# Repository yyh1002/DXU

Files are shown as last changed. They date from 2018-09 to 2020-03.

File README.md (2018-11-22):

# DXU - Dual Extrusion Upgrade for Ultimaker 2+

### DISCUSSION:
https://community.ultimaker.com/topic/24553-dxu-another-dual-extrusion-upgrade-for-um2/

### UPDATES:
- 19 Nov 2018 - Moved the lever dock from front to the back. 

### CREDITS:

##### Hardware:  
Lever action is inspired by Ultimaker 3.   
##### Firmware:   
Modified based on Mark2 version of Tinkergnome firmware by Tinkergnome.  
##### Software:   
Used Mark2Tweaks plugin for CURA by Krys Lawrence. CURA profiles are modified based on the Mark2 profiles by Tinkergnome and foehnsturm.

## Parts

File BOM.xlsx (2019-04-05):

Bill of Material 物料清单
物品/Material |  | 数量/Quantity | 链接/Link | 选项/Option | 备用链接/Alternative Link
胖子UM2 1.75热端新直通套件 | UM2 1.75 Hotend Kit (Heatsink, Bowden Coupler) | 2 | https://item.taobao.com/item.htm?spm=a1z10.5-c.w4002-9918354853.34.576d75aec3Kk6M&id=521401997290 | 新直通套件 | https://www.aliexpress.com/store/product/3D-Printer-Upgrade-Ultimaker-2-UM2-Extended-Newest-Olsson-Block-Nozzle-Hot-end-Kit/1877169_32988128287.html
胖子UM2 1.75热端新直通加热块 | UM2 1.75 Hotend Heat Block | 2 | https://item.taobao.com/item.htm?spm=a1z10.5-c.w4002-9918354853.34.576d75aec3Kk6M&id=521401997290 | 新直通加热块
290度高温打印PI喉管垫片 2*4*1 | 290°C High Temp Print Hotend Insulator 2*4*1 | 2 | https://item.taobao.com/item.htm?spm=a1z10.5-c.w4002-9918354853.25.60724c2fxu3tfa&id=581596714621 | 小2*4*1
UM2加热棒 | UM2 Heater Cartridge | 2 | https://www.makerpoint.nl/nl/ultimaker-heater-cartridge-24v-35w-um2um2ext.html
UM2 PT100测温 | UM2 PT100 Sensor | 2 | https://www.makerpoint.nl/nl/ultimaker-pt100-b-sensor-glassfiber-um2um2ext.html
2*6.35四氟远程送料管 | 2*6.35 PTFE Bowden Tube | 2 | https://item.taobao.com/item.htm?spm=a1z10.5-c.w4002-9918354853.32.576d75aec3Kk6M&id=521852878986 | 2*6.35
6.35料管蓝白卡扣 | 6.35 Bowden Coupler | 2 | https://www.makerpoint.nl/nl/ultimaker-bowden-tube-clips-pack-ultimaker.html
1.75耗材挤出机 | 1.75 Filament Feeder | 2 | https://www.thingiverse.com/thing:2289203 | Use 2.85 version for 6.35 tube
NEMA17 42*48挤出机电机 | NEMA17 42*48 Stepper Motor | 1 | https://www.makerpoint.nl/nl/ultimaker-feeder-motor-um3-extended-assembly.html
3510 12v涡轮吹料风扇 | 3510 12v Blower Fan | 2 | https://au.mouser.com/ProductDetail/?qs=%2FW4LtXOBxKsfL3eA88psUg== |  | https://item.taobao.com/item.htm?id=538704495777&_u=t2dmg8j26111&qq-pf-to=pcqq.group
3010 5v热端散热风扇 | 3010 5v Hotend Cooling Fan | 1 | https://www.aliexpress.com/item/DC-Cooling-Fan-3010-Fan-30-30-10mm-3010-fans-5V-12V-24V-Suitable-for-extruders/32909524999.html | 3010-5v
直线轴承LM6LUU 6*12*35mm | Linear Bearing LM6LUU 6*12*35mm | 2 | https://sg.misumi-ec.com/vona2/detail/110302578040/
压缩弹簧 0.8*9*15 或近似（建议买几个不同粗细的） | Compression Spring 0.8*9*15 or similar | 1
M3*6平头螺丝 | M3*6 Countersunk Screw | 4 | https://www.mcmaster.com/92125A126
M3*16半圆头螺丝 | M3*16 Button Head Screw | 6 | https://www.mcmaster.com/92095A184
M3*20半圆头螺丝 | M3*20 Button Head Screw | 2 | https://www.mcmaster.com/92095A185
M3*35半圆头螺丝 | M3*35 Button Head Screw | 4 | https://www.mcmaster.com/92095A201
M3螺母 | M3 Nut | 8 | https://www.mcmaster.com/90592A085
M3*3顶丝 | M3*3 Set Screw Cup Head | 1 | https://www.mcmaster.com/91390A097

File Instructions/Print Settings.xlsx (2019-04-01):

Print Settings 打印设置
零件名称/Parts Name | 材料/Material | 层高/Layer Height | 外壁线数/Wall Line Count | 支撑/Support
01 Housing Front | PC or PA66 | 0.2 | 5 | NO
02 Housing Back
03 Fan Shroud 3510 |  |  |  | YES
04 Fan Cover 3010
11 Lever 1 |  | 0.1 | 5 | NO
12 Lever 2 |  |  |  | YES
13 Lever 3 |  |  |  | NO
21 Dock |  | 0.2 | 5 | NO
22 Dock liner | PLA |  |  | NO
31 Heater clamp a | PC or PA66 | 0.2 |  | NO
32 Heater clamp b
33 Hotend fan pusher

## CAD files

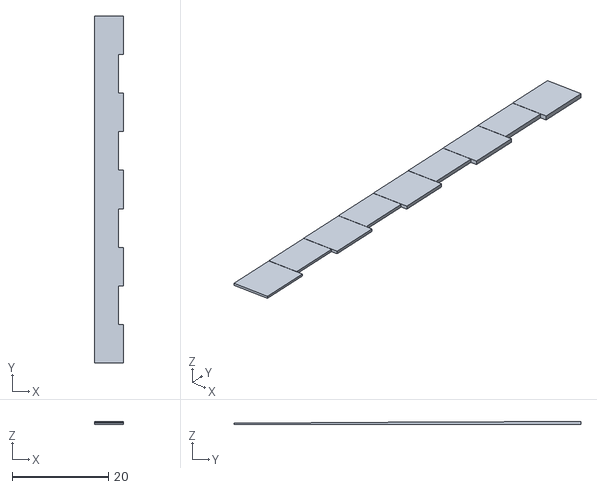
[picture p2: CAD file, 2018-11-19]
Calibration/Z-right.stl
6.00 x 72.0 x 0.66

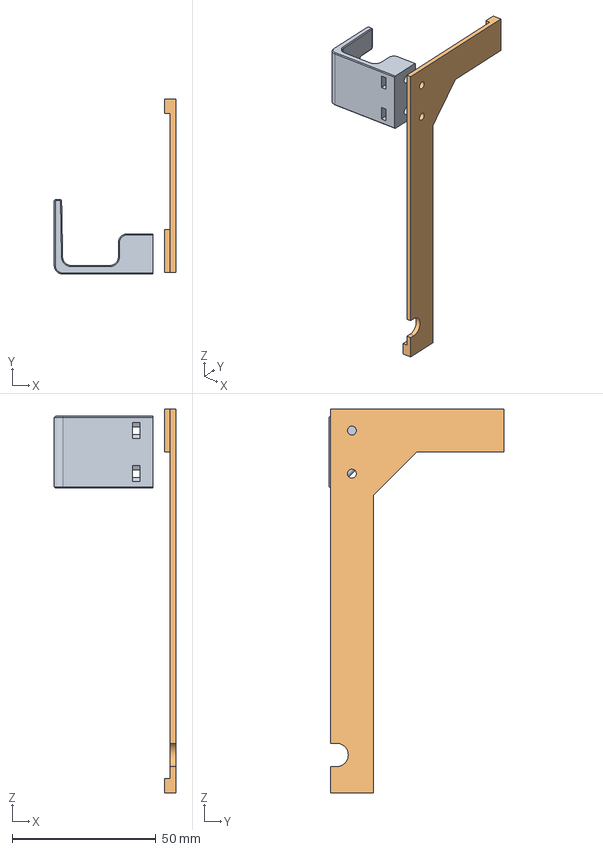
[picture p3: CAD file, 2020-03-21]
Parts file/Lever Dock Back.step
42.3 x 61.0 x 133.7 mm

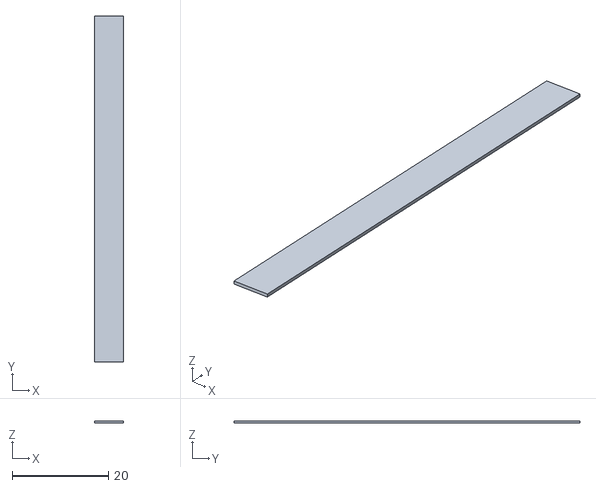
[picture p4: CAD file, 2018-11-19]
Calibration/Z-left.stl
6.00 x 72.0 x 0.5

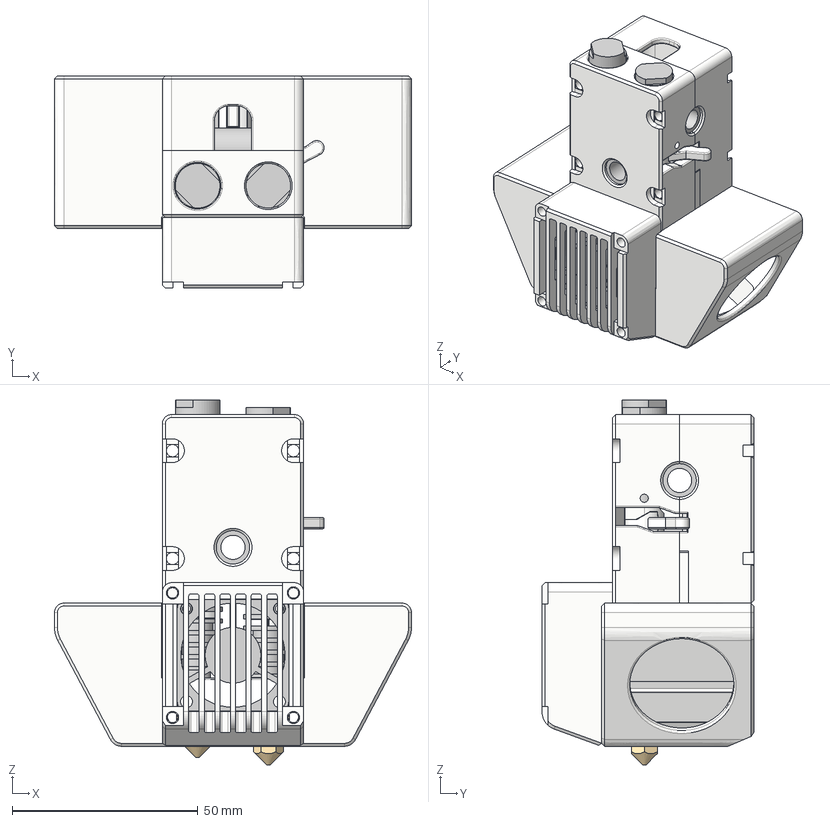
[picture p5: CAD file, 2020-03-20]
Parts file/DXU 1.5.step
96.0 x 57.0 x 98.1 mm
9434K51

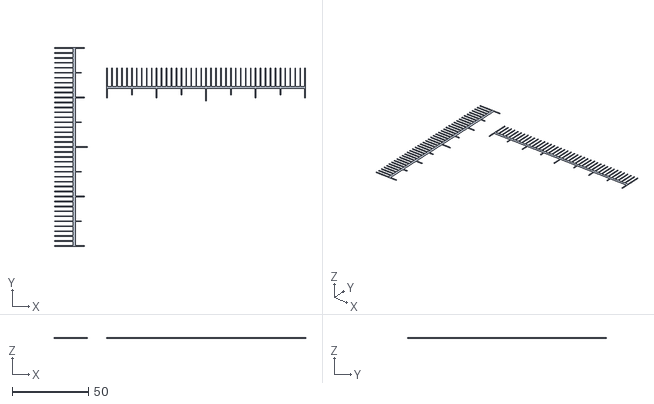
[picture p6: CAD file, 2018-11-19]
Calibration/xy_calibration_part_b.stl
164.3 x 130.1 x 0.3

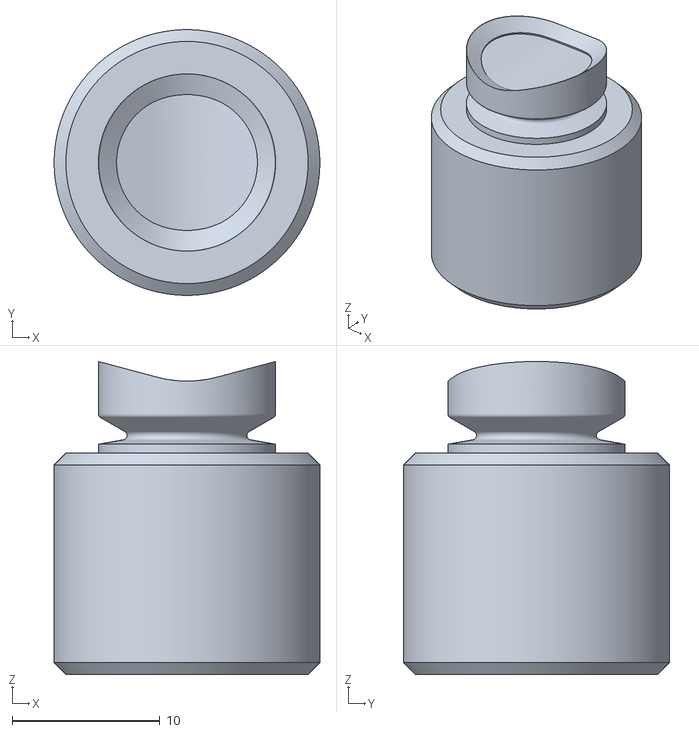
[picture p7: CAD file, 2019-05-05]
Parts file/46 Hole punch C.stl
18.0 x 18.0 x 21.2

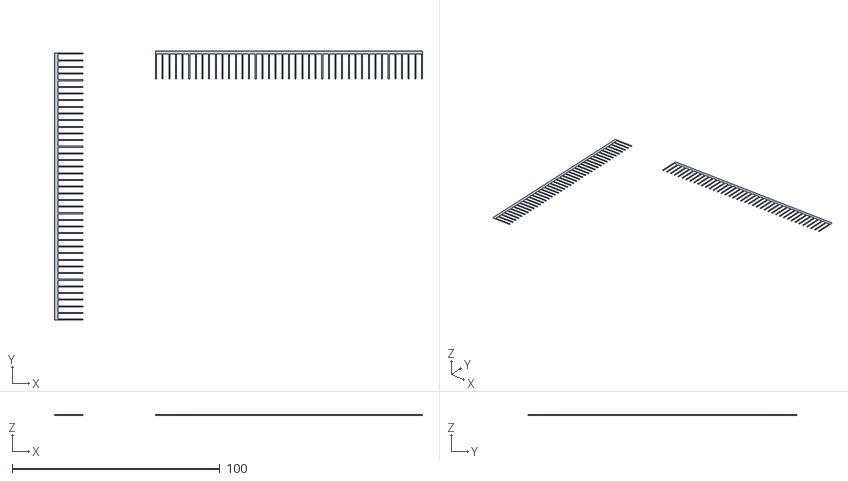
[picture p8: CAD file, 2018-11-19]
Calibration/xy_calibration_part_a.stl
177.1 x 129.6 x 0.3

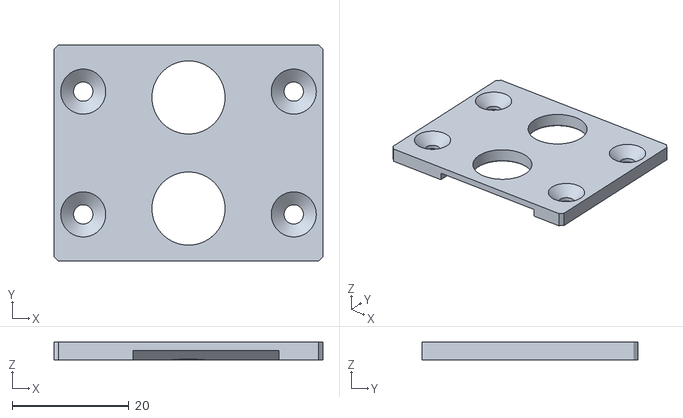
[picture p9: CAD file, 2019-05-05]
Parts file/44 Hole punch A.stl
46.0 x 37.0 x 3.00

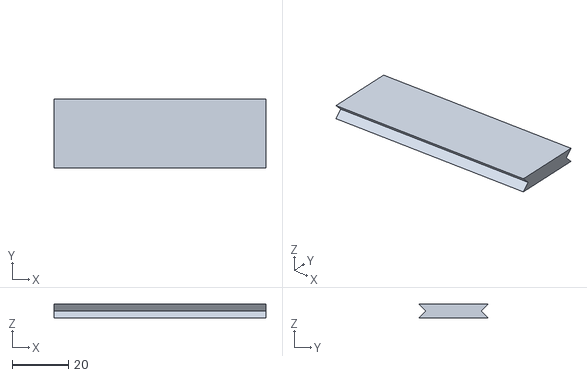
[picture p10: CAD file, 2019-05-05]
Parts file/41 Jig A.stl
75.3 x 24.5 x 4.80

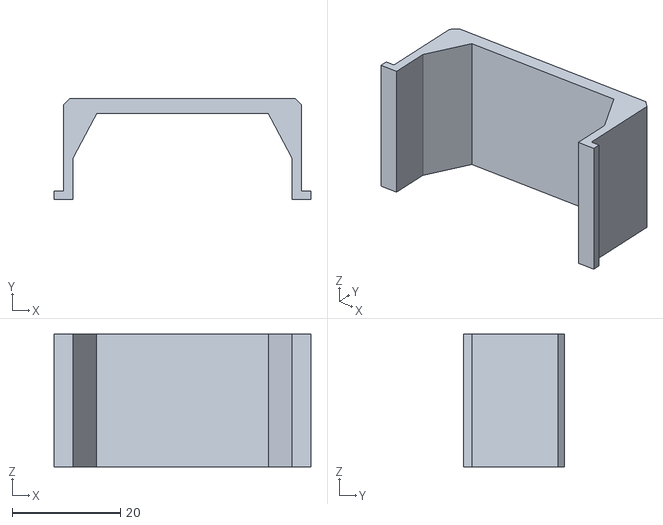
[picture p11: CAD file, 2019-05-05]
Parts file/42 Jig B.stl
47.4 x 18.6 x 24.5

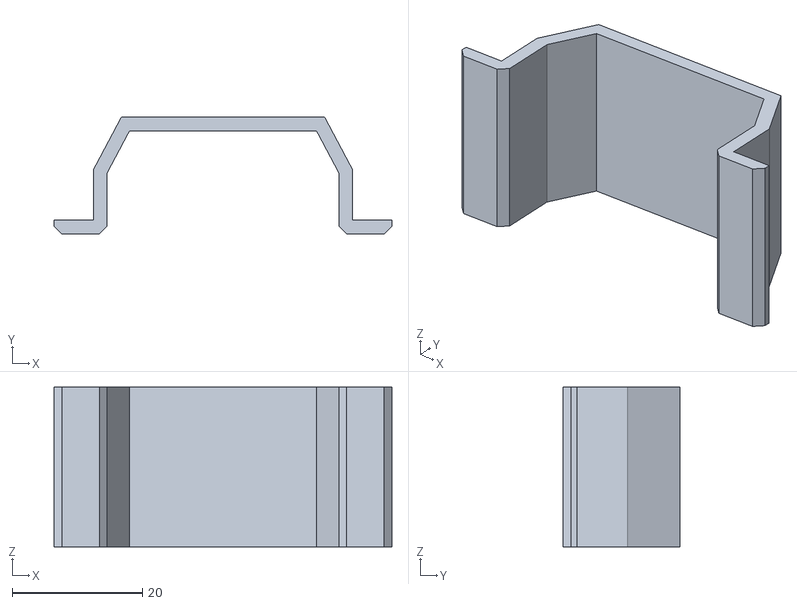
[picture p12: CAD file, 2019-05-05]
Parts file/43 Jig C.stl
51.8 x 17.9 x 24.5

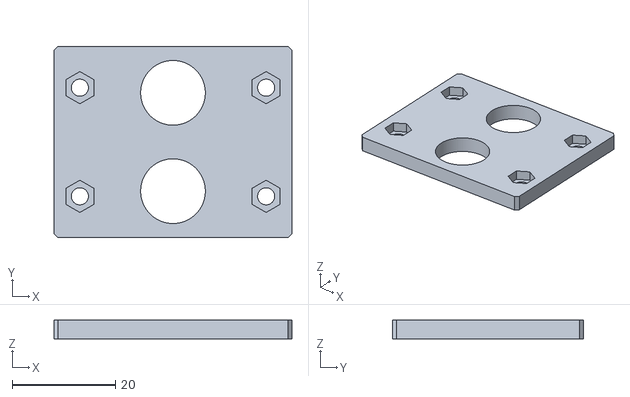
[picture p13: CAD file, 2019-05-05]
Parts file/45 Hole punch B.stl
46.0 x 37.0 x 3.60

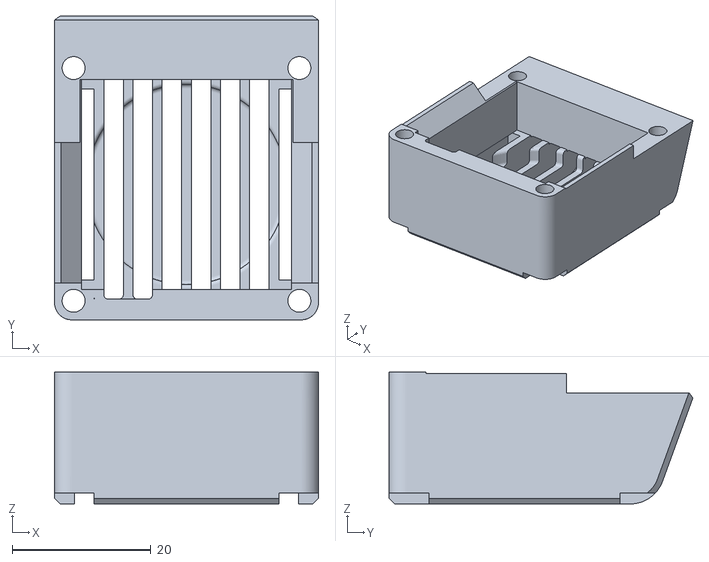
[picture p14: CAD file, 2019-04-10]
Parts file/04 Fan Cover 3010.stl
38.0 x 43.7 x 19.0

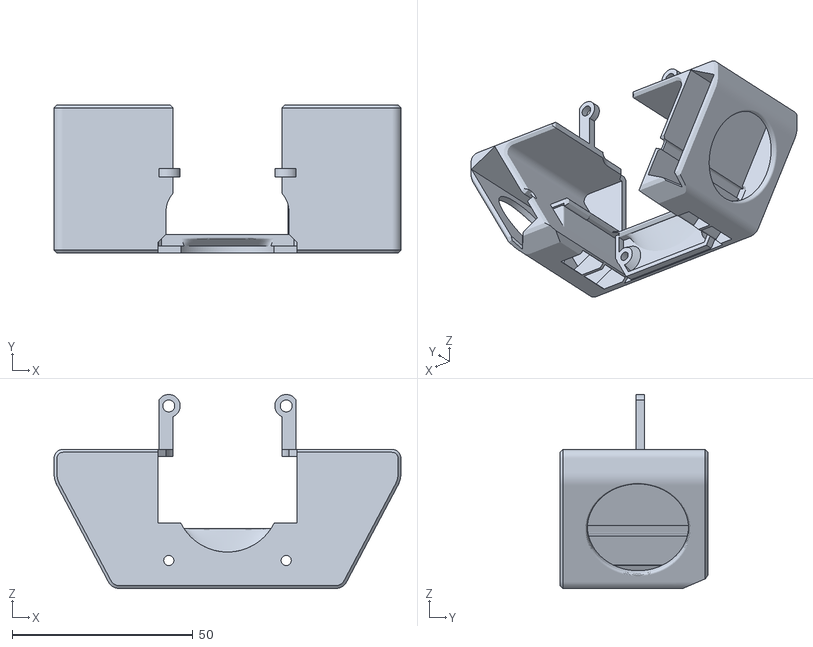
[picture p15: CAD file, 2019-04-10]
Parts file/03 Fan Shroud 3510.stl
96.0 x 41.0 x 53.7

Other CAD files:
Parts file/06 Fan Cover 2510.stl
Parts file/05 Fan Shroud 3015.stl
Parts file/02 Housing Back.stl
Parts file/13 Lever 3.stl
Parts file/01 Housing Front.stl
Parts file/11 Lever 1.stl
Parts file/12 Lever 2.stl
Parts file/21 Dock.stl
Parts file/22 Dock liner.stl
Parts file/31 Heater clamp a.stl
Parts file/32 Heater clamp b.stl
Parts file/33 Hotend fan pusher.stl

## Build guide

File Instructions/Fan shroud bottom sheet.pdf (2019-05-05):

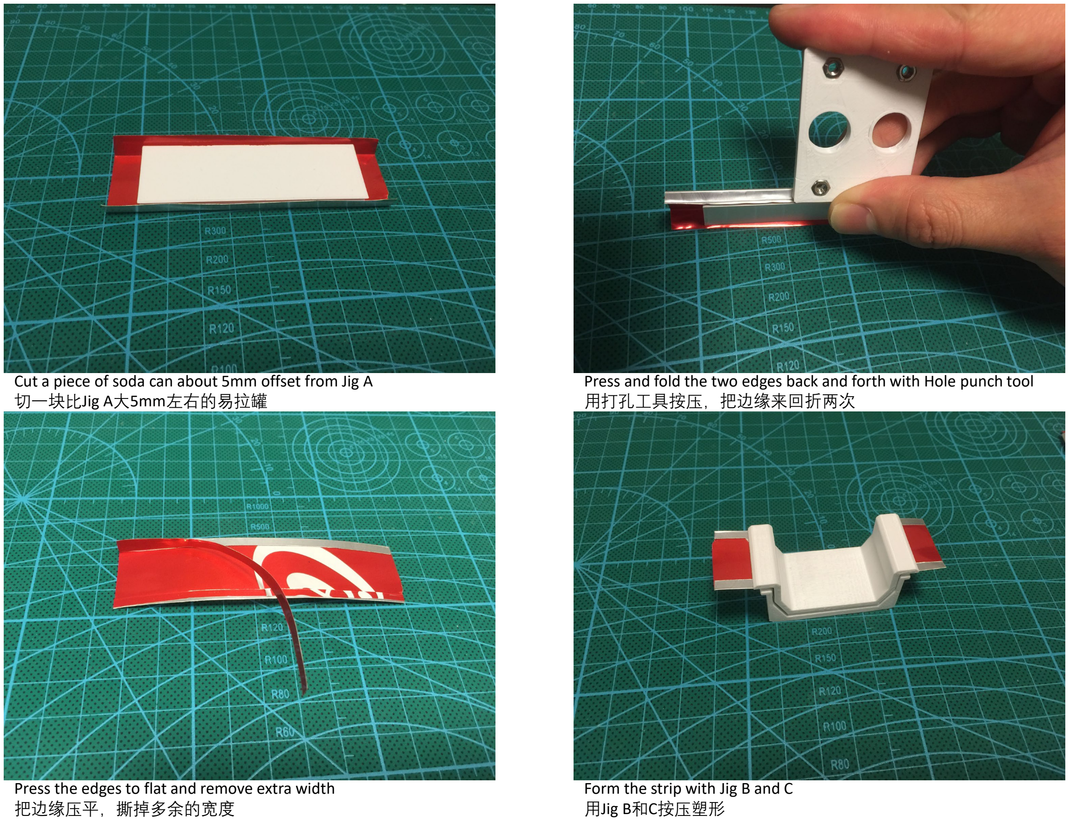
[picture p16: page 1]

Cut a piece of soda can about 5mm offset from Jig A 切一块比Jig A大5mm左右的易拉罐

Press and fold the two edges back and forth with Hole punch tool 用打孔工具按压，把边缘来回折两次

Press the edges to flat and remove extra width 把边缘压平，撕掉多余的宽度

Form the strip with Jig B and C 用Jig B和C按压塑形

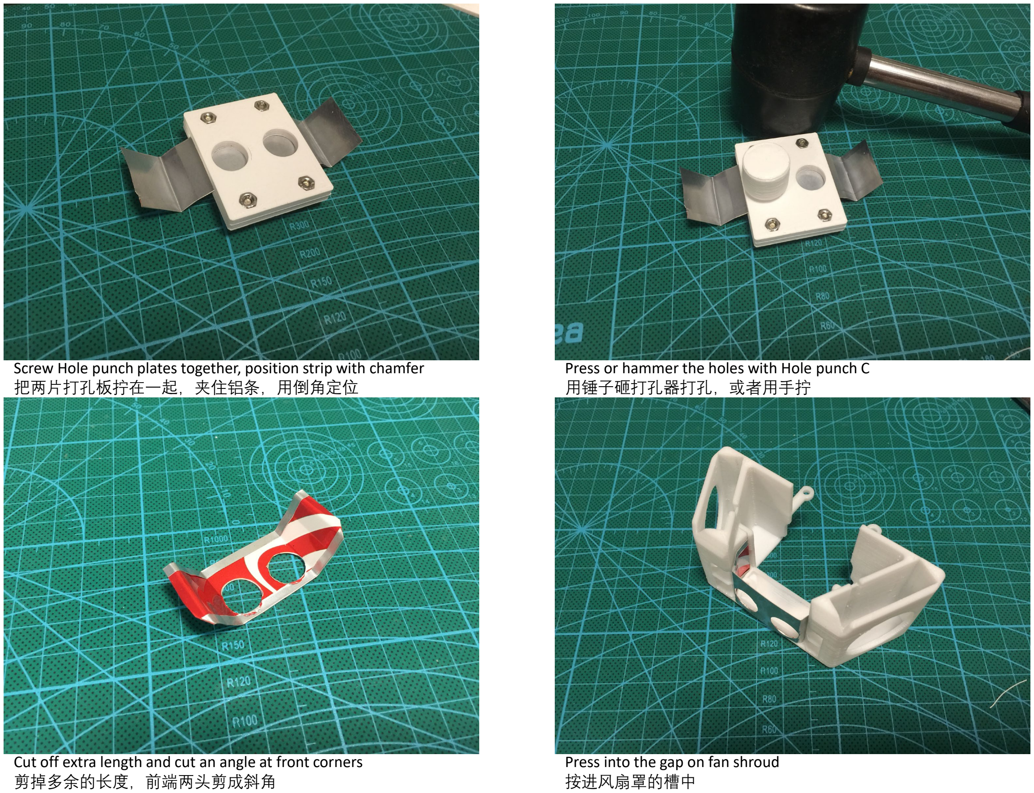
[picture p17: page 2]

Screw Hole punch plates together, position strip with chamfer 把两片打孔板拧在一起，夹住铝条，用倒角定位

Press or hammer the holes with Hole punch C 用锤子砸打孔器打孔，或者用手拧

Cut off extra length and cut an angle at front corners 剪掉多余的长度，前端两头剪成斜角

Press into the gap on fan shroud 按进风扇罩的槽中

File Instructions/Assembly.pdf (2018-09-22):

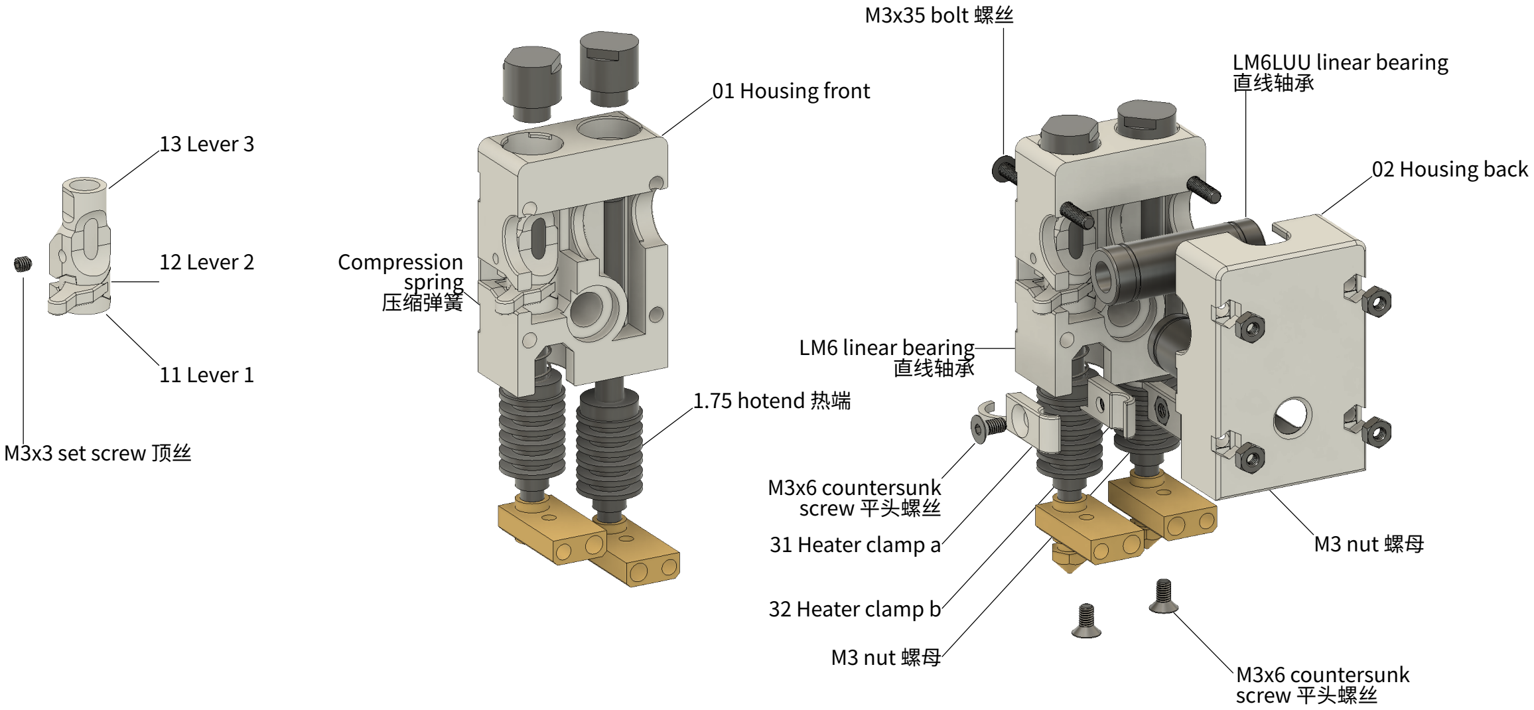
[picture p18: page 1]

13 Lever 3

01 Housing front
02 Housing back

1.75 hotend 热端

Compression spring 压缩弹簧

M3x35 bolt 螺丝

LM6 linear bearing 直线轴承

M3x6 countersunk
screw 平头螺丝

M3x6 countersunk
screw 平头螺丝

31 Heater clamp a
32 Heater clamp b
M3 nut 螺母

LM6LUU linear bearing
直线轴承

M3 nut 螺母

12 Lever 2

11 Lever 1
M3x3 set screw 顶丝

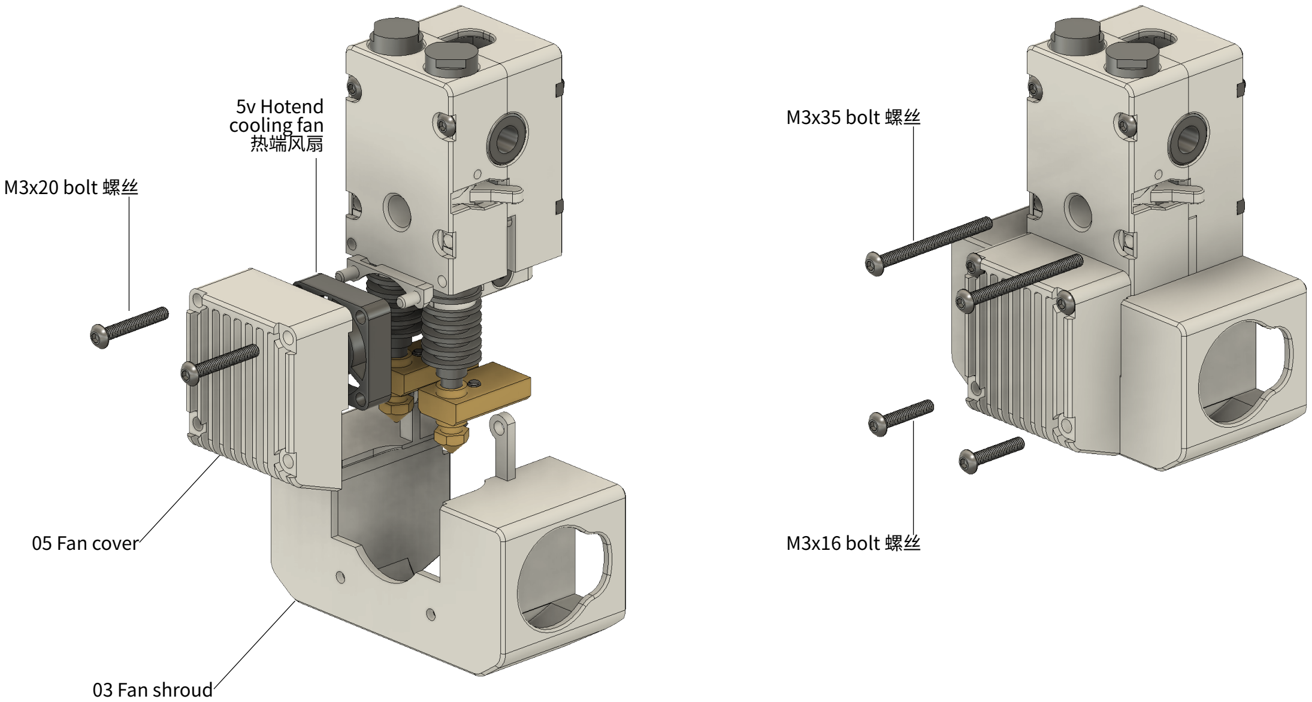
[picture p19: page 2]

05 Fan cover

03 Fan shroud

M3x20 bolt 螺丝

5v Hotend
cooling fan 热端风扇

M3x35 bolt 螺丝

M3x16 bolt 螺丝

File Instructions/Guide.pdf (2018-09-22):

DXU 双头升级步骤
1. 组装硬件
a. 购买零件—— 参考物料清单（BOM）
b. 打印部件—— 参考打印推荐设置（Printsettings.xlsx）。需要能够打印高温料的打印机
c. 拆解安装—— 打印头参考组装图纸（Assembly.pdf）。使用 Dockliner.stl 在机身右侧用 3mm 木工钻钻两个眼，用来固定扳手座。
2. 刷新固件
a. 上传固件—— 使用 CURA 上传编译好的固件，标准高度版为 DXU_firmware.hex，加高版为 DXU_Extended_firmware.hex
b. 校准换头位置—— 把打印头上的扳手搬到背部，右头下降的情况下，进入固件调整换头位置
c. 校准双头错位差—— 菜单中粗略设置右头高度，打印 Calibration 文件夹中的 XY_calibration.gcode 以及 Z-calibration.gcode 校准双喷嘴。校 准方法参考 https://magnetic-tool-changer.com/step-6-calibration.html
3. 安装软件
a. 安装 CURA 及插件
安装 CURA3.4 之后，把 Cura resources\3.4 文件夹中的文件复制到 C:\Users\*用户名*\AppData\Roaming\cura\3.4 把 Cura resources\plugins 文件夹中的文件复制到 C:\Program Files\Ultimaker Cura 3.4\plugins
b. 添加相应机型
i. 运行 CURA，添加打印机，选中 DXU，取名 DXU Dual

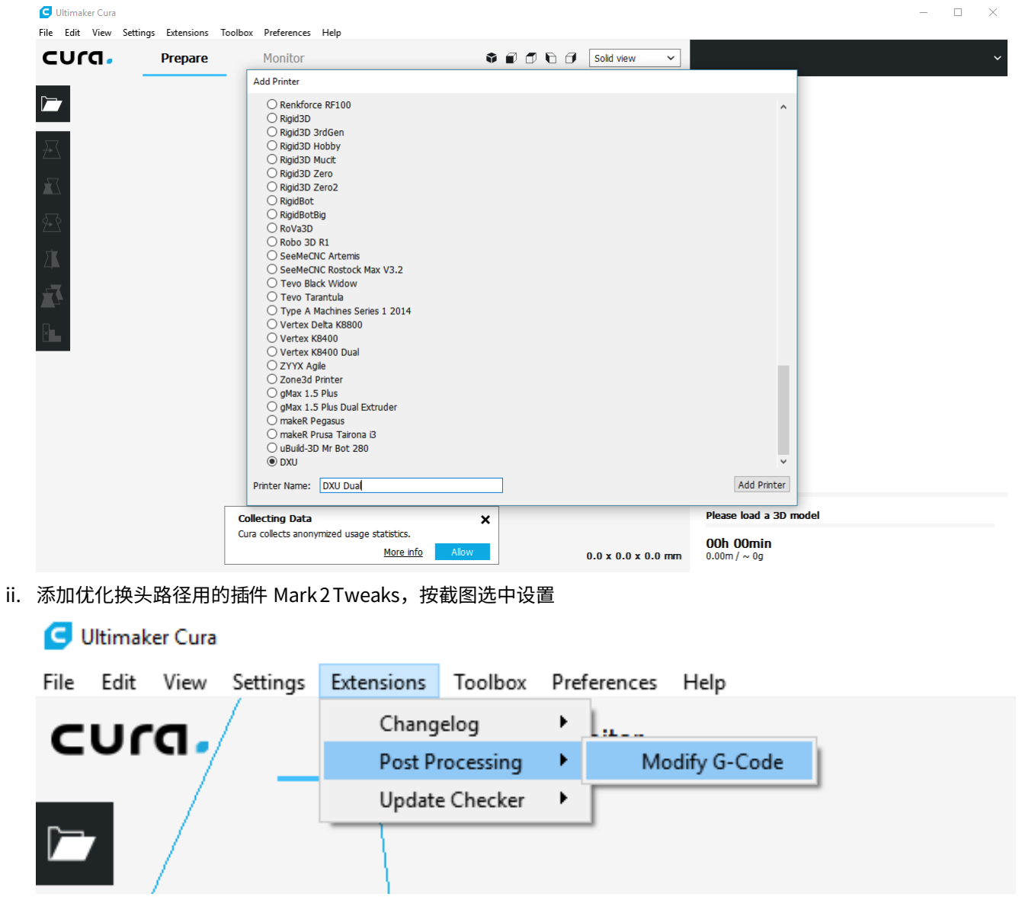
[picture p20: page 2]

ii. 添加优化换头路径用的插件 Mark 2 Tweaks，按截图选中设置

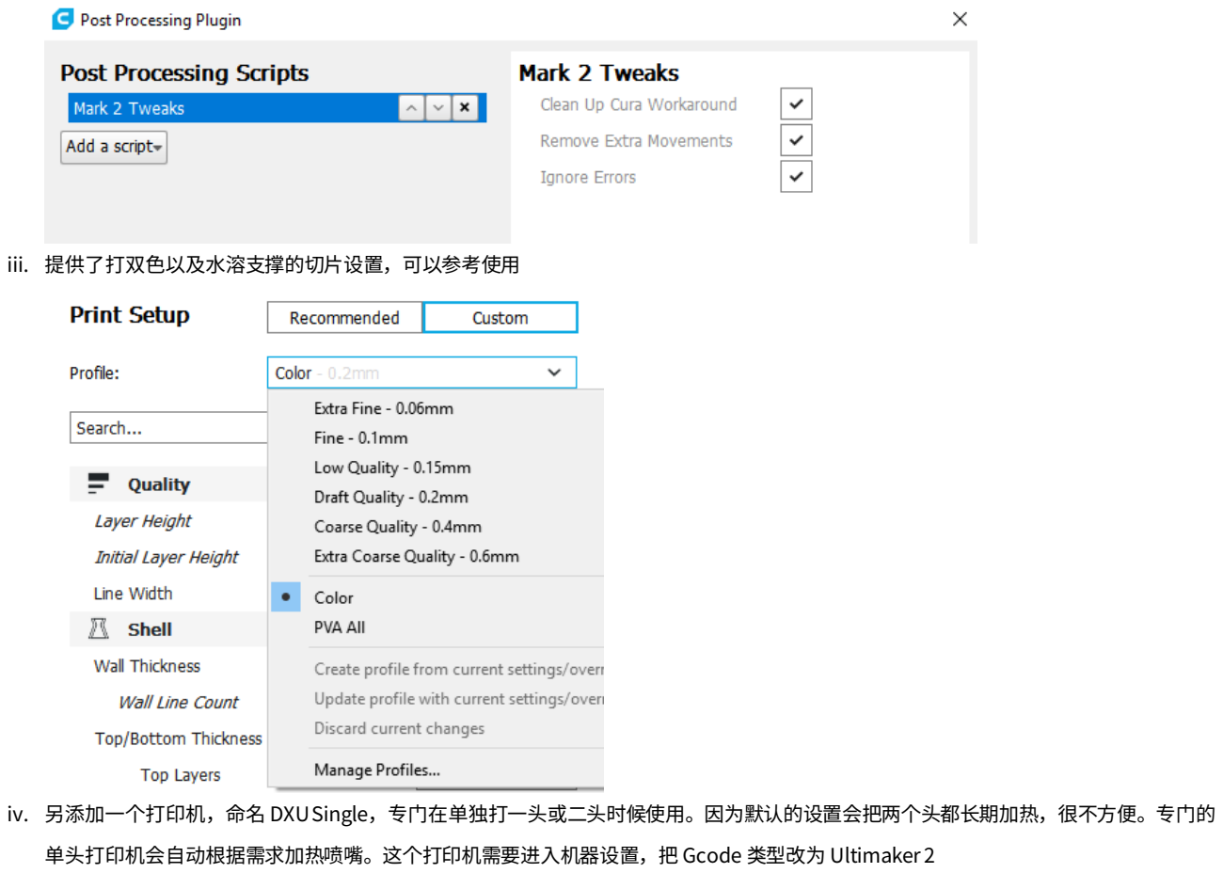
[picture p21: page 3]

iii. 提供了打双色以及水溶支撑的切片设置，可以参考使用

iv. 另添加一个打印机，命名 DXUSingle，专门在单独打一头或二头时候使用。因为默认的设置会把两个头都长期加热，很不方便。专门的 单头打印机会自动根据需求加热喷嘴。这个打印机需要进入机器设置，把 Gcode 类型改为 Ultimaker 2

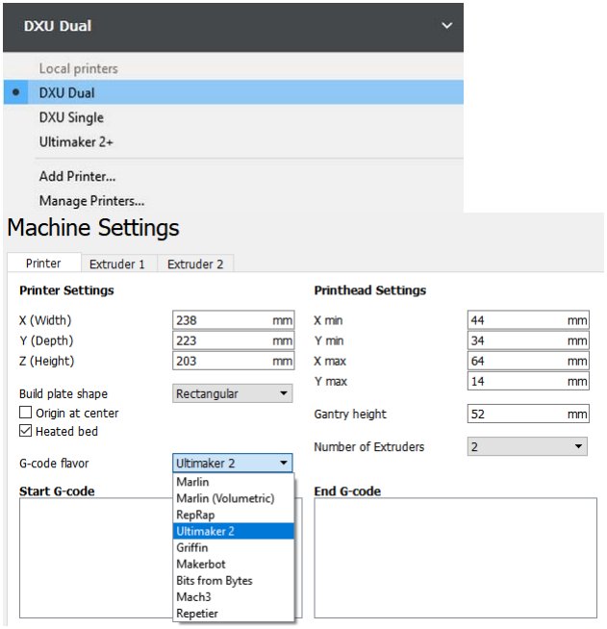
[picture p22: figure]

v. 可打印区域会根据喷嘴使用自动调整

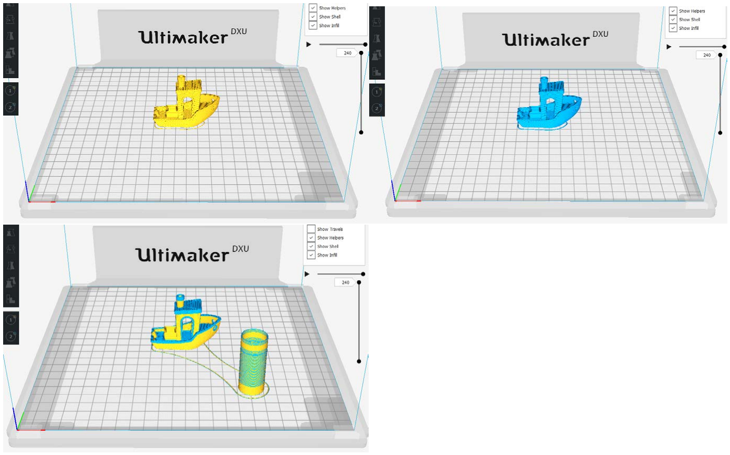
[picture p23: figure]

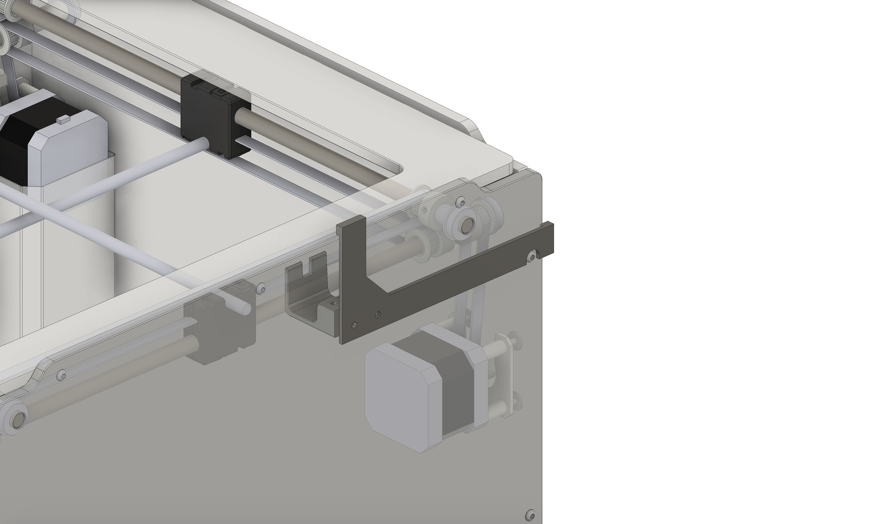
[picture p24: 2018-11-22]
Instructions/Use of Dock liner 1.1.jpg

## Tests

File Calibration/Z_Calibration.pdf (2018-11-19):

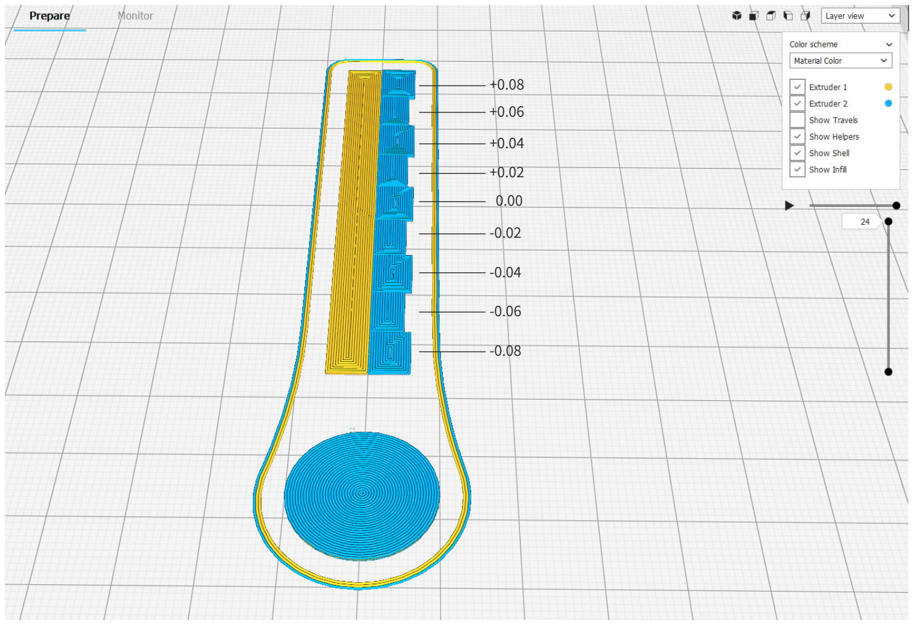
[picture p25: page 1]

0.00
-0.02
-0.04
-0.06
-0.08

+0.02

+0.04

+0.06

+0.08

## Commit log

2019-04-01 v1.5 firmware update
    [Configuration.h, ConfigurationDual.h, Configuration_adv.h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]
2019-04-02 Corrected wrong fan link
    [BOM.xlsx]
2019-04-03 Previous fan support
    [05 Fan Shroud 3015.stl, 06 Fan Cover 2510.stl]
2019-04-05 Update 3510 fan link
    [BOM.xlsx]
2019-04-10 Improved part cooling
    [03 Fan Shroud 3510.stl, 04 Fan Cover 3010.stl]
2019-05-05 Jig for fan shroud
    [41 Jig A.stl, 42 Jig B.stl, 43 Jig C.stl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]
2019-05-05 Create Fan shroud bottom sheet.pdf
2020-02-20 Cura 4.5 profile
    [dxu.cfg]
2020-03-20 Create DXU 1.5.step
    [DXU 1.5.step]
2020-03-21 Create Lever Dock Back.step
    [Lever Dock Back.step]
